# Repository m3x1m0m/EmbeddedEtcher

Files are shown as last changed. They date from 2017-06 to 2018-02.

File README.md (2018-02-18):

# Embedded Etcher
Design files related to a photo-sensitive layering method etching machine
everyone can build to produce prototypes quickly at home or in the lab.

## Architecture 
The etching machine consists basically out of two parts. The
first part is a UV light, which is used to develop a photo-sensitive PCB. Once
this has been done.  The PCB has to be treated with sodium hydroxide (NaOH)
dissolved in water. This removes the UV-sensitive plastic, where it has been
tackeled by the light. 

The second part is the actual etching machine, which is designed to be
compatible to euro cards (and even bigger ones). The etching machine is either
filled with sodium persulfate (Na<sub>2</sub>S<sub>2</sub>O<sub>8</sub>) or
iron(III) chloride (FeCl<sub>3</sub>) dissolved in water of course.

## RedheadOS

One of the byproducts of this project is a small real-time OS, which is ment to run on embedded platforms. It is based on fixed priority scheduling and includes some nice accessories, so one does not always have to reinvent the wheel for every new project.  

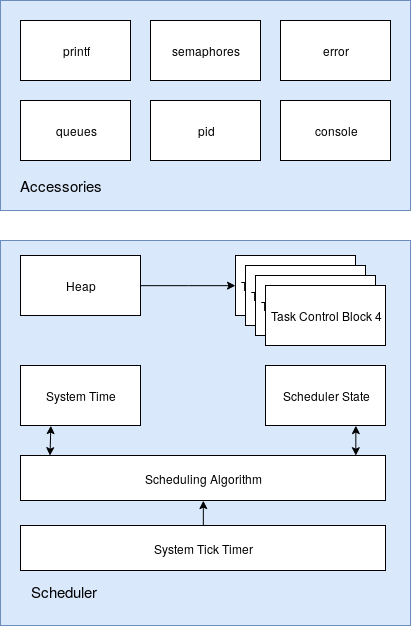
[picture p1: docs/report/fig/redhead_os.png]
ReadheadOS Structure.


## UV Light 

### Driver Extension Board

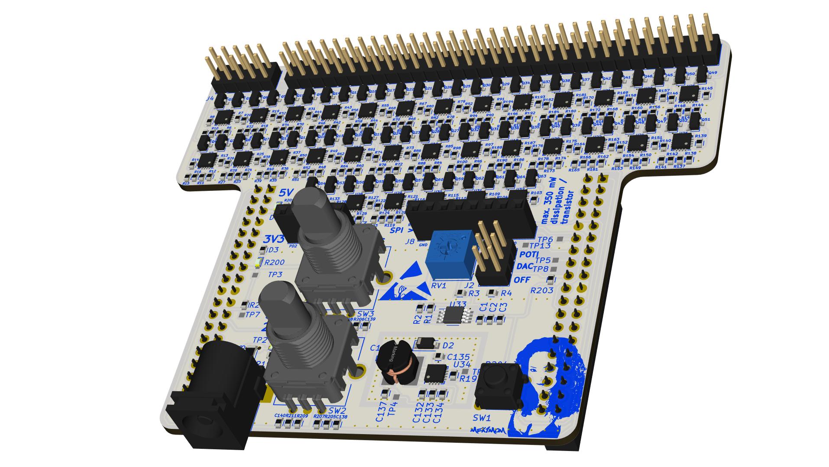
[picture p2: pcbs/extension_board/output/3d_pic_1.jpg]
3D Preview from KiCad (1).


This PCB is made to fit the [Nucleo-F103RB](http://www.st.com/en/evaluation-tools/nucleo-f103rb.html)
development board from STM. Features:
* 64 LED driver stages.
* 6.4 A (0.1 A per stage) and 24 V max. input.
* 0.2 A max. and 350 mW dissipation max. per stage. Stages can be left floating if unused without
the threat of damaging the device.
* 10 Bit Digital-to-Analog Converter (DAC) to steer the driver combined with feedback amplification
to achieve a tremendously fine resolution.
* Optional potentiometer to set the current.
* Control loop to guarantee the desired current and respond quickly to changing the setpoint.
* 2 rotary encoders and 1 tactile switch.
* I2C header.
* SPI header.
 
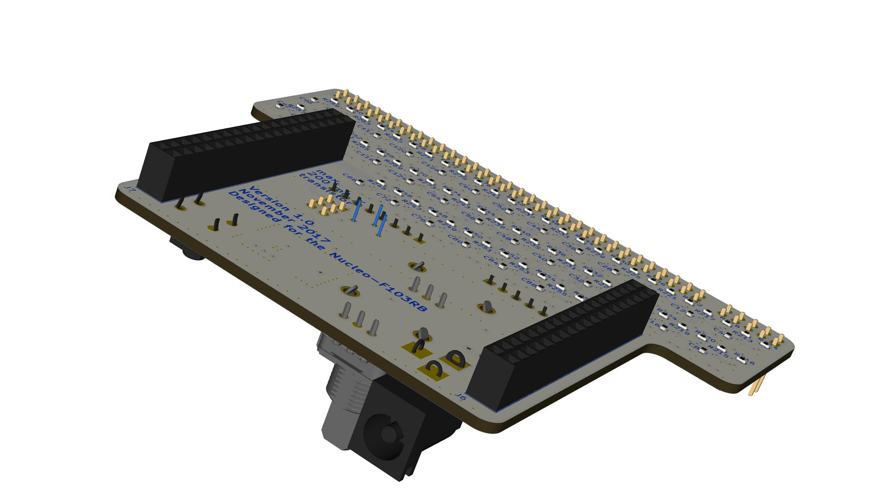
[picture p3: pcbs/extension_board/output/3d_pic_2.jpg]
3D Preview from KiCad (2).

  
  It is important to mention, that the resistors for the non-inverting amplifier
  in the feedback loop are optimized to result in a maximum current of 33 mA for
  3.3 V in order to achieve higher currents different resistor values have to be
  chosen.   
  
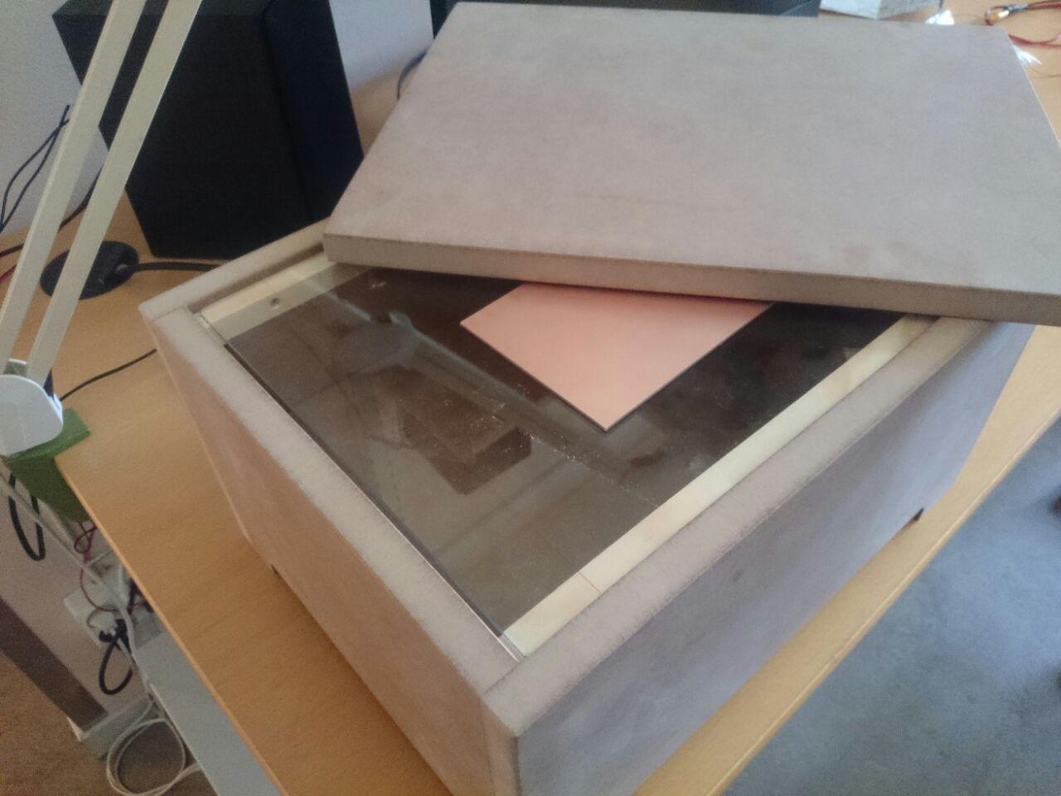
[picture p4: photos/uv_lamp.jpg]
UV Lamp
   

## Cuvette 

The cuvette can be handcrafted. It is possible to buy the five glass pieces need
at a glassers shop or to cut it oneself. The glass parts can be glued together with
silicon.  
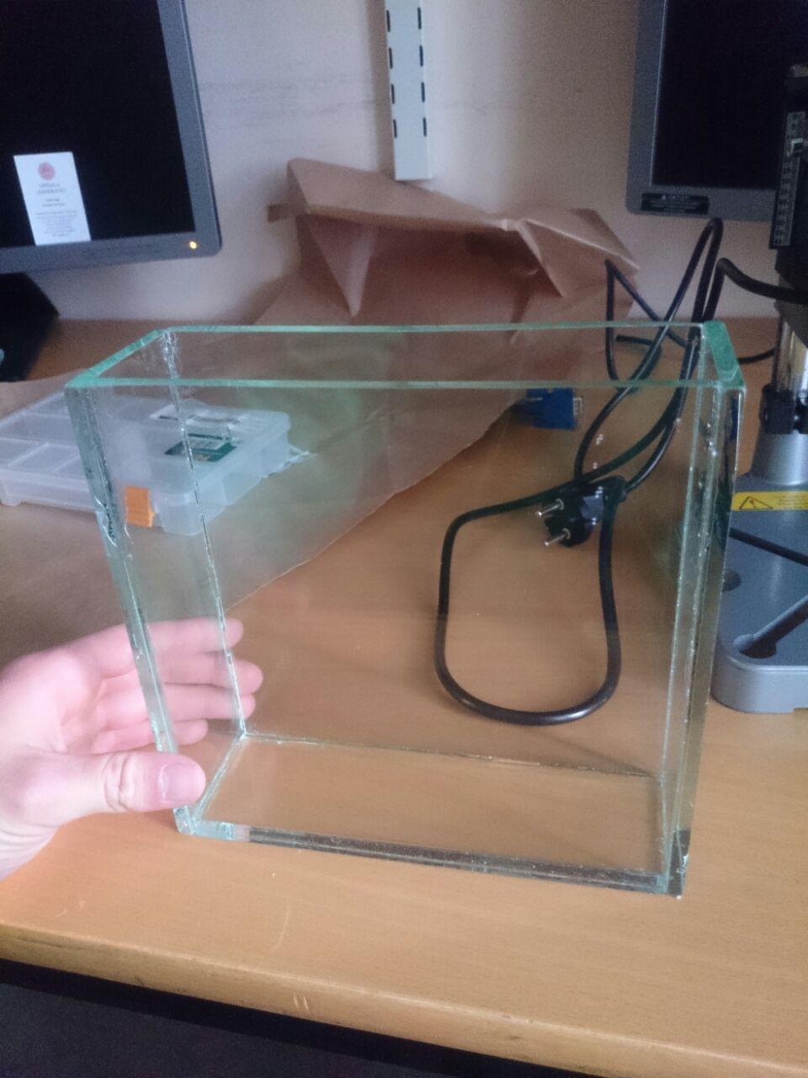
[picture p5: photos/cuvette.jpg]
Cuvette


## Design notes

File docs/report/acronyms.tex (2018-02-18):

%%%%%%%%%%%%%%%%%%%%%%%%%%%%%%%%%%%%%%%%%%%%%%%%%%%%%%%%%%%%%%%%%%%%%%%%%%%%%%%%%%%%%%
%% Author:      Nils Weber and Maximilian Stiefel
%% Date:        23.12.2017
%% University:  Uppsala Universitet
%% Department:  Institutionen för informationsteknologi 
%% Course:      Embedded Control System Project
%% Project:     PRECISELY CONTROLLED DIY ETCHING MACHINE 
%%				FOR USAGE AT HOME AND IN SMALL LABS
%%%%%%%%%%%%%%%%%%%%%%%%%%%%%%%%%%%%%%%%%%%%%%%%%%%%%%%%%%%%%%%%%%%%%%%%%%%%%%%%%%%%%%

\newacronym[firstplural={Printed Circuit Boards (PCBs)},plural={PCBs}]{PCB}{PCB}{Printed Circuit Board}
\newacronym[firstplural={Light Emitting Diodes (LEDs)},plural={LEDs}]{LED}{LED}{Light Emitting Diode}
\newacronym[firstplural={Integrated Development Environments (IDEs)},plural={IDEs}]{IDE}{IDE}{Integrated Development Environment}
\newacronym[firstplural={Task Control Blocks (TCBs)},plural={TCBs}]{TCB}{TCB}{Task Control Block}

\newacronym{DIY}{DIY}{Do It Yourself}
\newacronym{ECAD}{ECAD}{Electronic Computer-Aided Design}
\newacronym{UV}{UV}{Ultraviolet}
\newacronym{DC}{DC}{Direct Current}
\newacronym{PWM}{PWM}{Pulse-Width Modulation}
\newacronym{EMI}{EMI}{Electromagnetic Interference}
\newacronym{SPI}{SPI}{Serial Peripheral Interface}
\newacronym{I2C}{I2C}{Inter-Integrated Circuit}
\newacronym{OLED}{OLED}{Organic \gls{LED}}
\newacronym[firstplural={Operating Systems (OS)},plural={OS}]{OS}{OS}{Operating System}
\newacronym{DAC}{DAC}{Digital-to-Analog Converter}
\newacronym{ADC}{ADC}{Analog-to-Digital Converter}
\newacronym{IC}{IC}{Integrated Circuit}
\newacronym{NTC}{NTC}{Negative Temperature Coefficient}
\newacronym{PID}{PID}{Proportional Integral Differential}
\newacronym{USART}{USART}{Universal Asynchronous/Synchronous Receiver/Transmitter}
\newacronym{EEPROM}{EEPROM}{Electrically Erasable Programmable Read-Only Memory}
\newacronym{GNU}{GNU}{GNU's Not Unix!}
\newacronym{IRQ}{IRQ}{Interrupt Request}
\newacronym{FDM}{FDM}{Fused Deposition Modeling}

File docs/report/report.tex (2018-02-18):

%%%%%%%%%%%%%%%%%%%%%%%%%%%%%%%%%%%%%%%%%%%%%%%%%%%%%%%%%%%%%%%%%%%%%%%%%%%%%%%%%%%%%%
%% Author:      Nils Weber and Maximilian Stiefel
%% Date:        23.12.2017
%% University:  Uppsala Universitet
%% Department:  Institutionen för informationsteknologi 
%% Course:      Embedded Control System Project
%% Project:     PRECISELY CONTROLLED DIY ETCHING MACHINE 
%%				FOR USAGE AT HOME AND IN SMALL LABS
%%%%%%%%%%%%%%%%%%%%%%%%%%%%%%%%%%%%%%%%%%%%%%%%%%%%%%%%%%%%%%%%%%%%%%%%%%%%%%%%%%%%%%

\documentclass{report}

%%%%%%%%%%%%%%%%%%%%%%%%%%%%%%%%%%%%%%%%%%%%%%%%%%%%%%%%%%%%%%%%%%%%%%%%%%%%%%%%%%%%%%
% Preamble
%%%%%%%%%%%%%%%%%%%%%%%%%%%%%%%%%%%%%%%%%%%%%%%%%%%%%%%%%%%%%%%%%%%%%%%%%%%%%%%%%%%%%%

% Encoding of the input
\usepackage[utf8]{inputenc}

% Geometry stuff
\usepackage[head=24pt,a4paper,lmargin={2.5cm},rmargin={2.5cm},tmargin={2.5cm},
bmargin={2.5cm}]{geometry}

% For graphics
\usepackage{graphicx}
\usepackage{float}

% For code highlighting
\usepackage{minted}

% For shaded
\usepackage{xcolor}
\usepackage{framed}
\definecolor{shadecolor}{gray}{0.9}

% For some symbols
\usepackage{textcomp}
%\usepackage{eurosans}

% For math
\usepackage{amssymb}
\usepackage{amsmath}

\setlength{\parindent}{0em} 

% For title formatting 
\usepackage{titlesec} 

\titleformat%
{\chapter}%
[block]%
{\bfseries\Huge}%
{\thechapter\hspace{1cm}}%
{0pt}%
{\bfseries\Huge}%

% For SI units.
\usepackage{siunitx}

% Input definition macros
\input{mydefs.tex}

\usepackage{hyperref}
\hypersetup{
	plainpages=false,
	unicode=false,
	pdftoolbar=true,
	pdfmenubar=true,
	pdffitwindow=false,
	pdfstartview={FitH},
	pdftitle={\mytitle},
	pdfauthor={\myauthora ,\space\myauthorb},
	pdfsubject={\mytypeofwork\space\myduedate},
	pdfcreator={\myauthora ,\space\myauthorb},
	pdfproducer={\myauthora ,\space\myauthorb},
	pdfkeywords={\mykeywords},
	pdfnewwindow=true,
	pdfborder={0 0 0},
	colorlinks=false,
	linkcolor=black,
	citecolor=black,
	filecolor=black,
	urlcolor=cyan
}	

\newcommand{\newpar}{\vspace{1em}\\}
\newcommand{\myemph}[1]{\textsl{#1}}

% For PDFs
\usepackage{pdfpages}

% For quotes
\usepackage[autostyle]{csquotes}
\usepackage[style=ieee,backend=bibtex]{biblatex}
\addbibresource{literature.bib}

% For tables
\usepackage{tabularx}
% For a forced linebreak in a table cell 
% cf. https://tex.stackexchange.com/questions/2441/how-to-add-a-forced-line-break-inside-a-table-cell#19678
\newcommand{\specialcell}[2][c]{%
  \begin{tabular}[#1]{@{}c@{}}#2\end{tabular}}

% For glossary
\usepackage[toc,nonumberlist]{glossaries} 
\makeglossaries     
\input{./acronyms.tex}

% For chemical formulas
\usepackage{chemformula}

% Header and footer
\usepackage{fancyhdr}
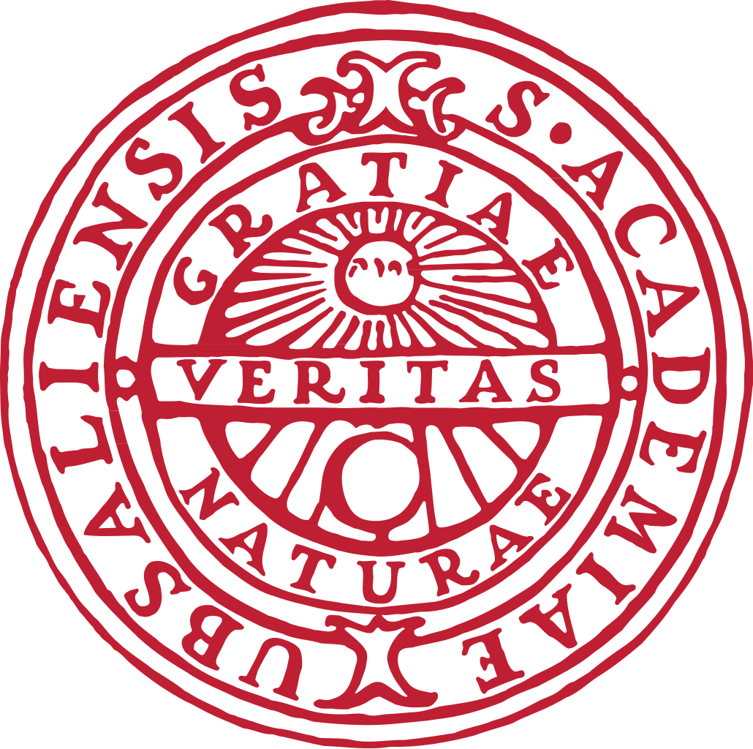
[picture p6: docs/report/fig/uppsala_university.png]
\lhead{\ifnum\value{chapter}>0  \fi}
\chead{}
\rhead{\ifnum\value{chapter}>0 
\leftmark{} |
\rightmark{}
\fi}
\lfoot{}
\cfoot{\thepage}
\rfoot{}
%\setlength{\headheight}{1cm}

\begin{document}

%%%%%%%%%%%%%%%%%%%%%%%%%%%%%%%%%%%%%%%%%%%%%%%%%%%%%%%%%%%%%%%%%%%%%%%%%%%%%%%%%%%%%%
% Titlepage
%%%%%%%%%%%%%%%%%%%%%%%%%%%%%%%%%%%%%%%%%%%%%%%%%%%%%%%%%%%%%%%%%%%%%%%%%%%%%%%%%%%%%%
\input{titlepage.tex}

\newcounter{roman}
\pagenumbering{Roman}

\pagestyle{fancy}

%%%%%%%%%%%%%%%%%%%%%%%%%%%%%%%%%%%%%%%%%%%%%%%%%%%%%%%%%%%%%%%%%%%%%%%%%%%%%%%%%%%%%%
% TOC etc.
%%%%%%%%%%%%%%%%%%%%%%%%%%%%%%%%%%%%%%%%%%%%%%%%%%%%%%%%%%%%%%%%%%%%%%%%%%%%%%%%%%%%%%
\tableofcontents
\listoffigures
\newpage
\listoftables
\printglossary[title=List of Abbreviations,toctitle=List of Abbreviations,type=\acronymtype]

\newpage
\setcounter{roman}{\value{page}}
\pagenumbering{arabic}
\setcounter{page}{1}

%%%%%%%%%%%%%%%%%%%%%%%%%%%%%%%%%%%%%%%%%%%%%%%%%%%%%%%%%%%%%%%%%%%%%%%%%%%%%%%%%%%%%%
% Introduction
%%%%%%%%%%%%%%%%%%%%%%%%%%%%%%%%%%%%%%%%%%%%%%%%%%%%%%%%%%%%%%%%%%%%%%%%%%%%%%%%%%%%%%

\input{./doc/introduction.tex}

%%%%%%%%%%%%%%%%%%%%%%%%%%%%%%%%%%%%%%%%%%%%%%%%%%%%%%%%%%%%%%%%%%%%%%%%%%%%%%%%%%%%%%
% Background and Analysis
%%%%%%%%%%%%%%%%%%%%%%%%%%%%%%%%%%%%%%%%%%%%%%%%%%%%%%%%%%%%%%%%%%%%%%%%%%%%%%%%%%%%%%

\input{./doc/background.tex}

%%%%%%%%%%%%%%%%%%%%%%%%%%%%%%%%%%%%%%%%%%%%%%%%%%%%%%%%%%%%%%%%%%%%%%%%%%%%%%%%%%%%%%
% Design
%%%%%%%%%%%%%%%%%%%%%%%%%%%%%%%%%%%%%%%%%%%%%%%%%%%%%%%%%%%%%%%%%%%%%%%%%%%%%%%%%%%%%%

\input{./doc/design.tex}

%%%%%%%%%%%%%%%%%%%%%%%%%%%%%%%%%%%%%%%%%%%%%%%%%%%%%%%%%%%%%%%%%%%%%%%%%%%%%%%%%%%%%%
% Implementation
%%%%%%%%%%%%%%%%%%%%%%%%%%%%%%%%%%%%%%%%%%%%%%%%%%%%%%%%%%%%%%%%%%%%%%%%%%%%%%%%%%%%%%

\input{./doc/implementation.tex}

%%%%%%%%%%%%%%%%%%%%%%%%%%%%%%%%%%%%%%%%%%%%%%%%%%%%%%%%%%%%%%%%%%%%%%%%%%%%%%%%%%%%%%
% Evaluation
%%%%%%%%%%%%%%%%%%%%%%%%%%%%%%%%%%%%%%%%%%%%%%%%%%%%%%%%%%%%%%%%%%%%%%%%%%%%%%%%%%%%%%

\input{./doc/evaluation.tex}

%%%%%%%%%%%%%%%%%%%%%%%%%%%%%%%%%%%%%%%%%%%%%%%%%%%%%%%%%%%%%%%%%%%%%%%%%%%%%%%%%%%%%%
% Conclusion
%%%%%%%%%%%%%%%%%%%%%%%%%%%%%%%%%%%%%%%%%%%%%%%%%%%%%%%%%%%%%%%%%%%%%%%%%%%%%%%%%%%%%%

\input{./doc/conclusion.tex}

%%%%%%%%%%%%%%%%%%%%%%%%%%%%%%%%%%%%%%%%%%%%%%%%%%%%%%%%%%%%%%%%%%%%%%%%%%%%%%%%%%%%%%
% Bibliography and Appendix
%%%%%%%%%%%%%%%%%%%%%%%%%%%%%%%%%%%%%%%%%%%%%%%%%%%%%%%%%%%%%%%%%%%%%%%%%%%%%%%%%%%%%%

\clearpage
\pagenumbering{Roman}
\setcounter{page}{\value{roman}}
\pagestyle{empty}

\printbibliography[heading=bibintoc]

%%%%%%%%%%%%%%%%%%%%%%%%%%%%%%%%%%%%%%%%%%%%%%%%%%%%%%%%%%%%%%%%%%%%%%%%%%%%%%%%%%%%%%
% Appendix
%%%%%%%%%%%%%%%%%%%%%%%%%%%%%%%%%%%%%%%%%%%%%%%%%%%%%%%%%%%%%%%%%%%%%%%%%%%%%%%%%%%%%%
\appendix
% Introduce new geometry to be able to have more space for appendix
\newgeometry{lmargin={2.5cm},rmargin={2.5cm},tmargin={0cm},bmargin={1,5cm}}
\includepdf[pages={1},scale=0.8,pagecommand=\chapter{Schematics Extension Board}\label{append:extension}]{./fig/schematics_extension_board.pdf}
\includepdf[pages={2-3, 35-37},scale=0.8,pagecommand={}]{./fig/schematics_extension_board.pdf}

\chapter{Technical drawings of PCB-holder}
\label{append:techDrawPCB}

\begin{figure}[H]
\centering  
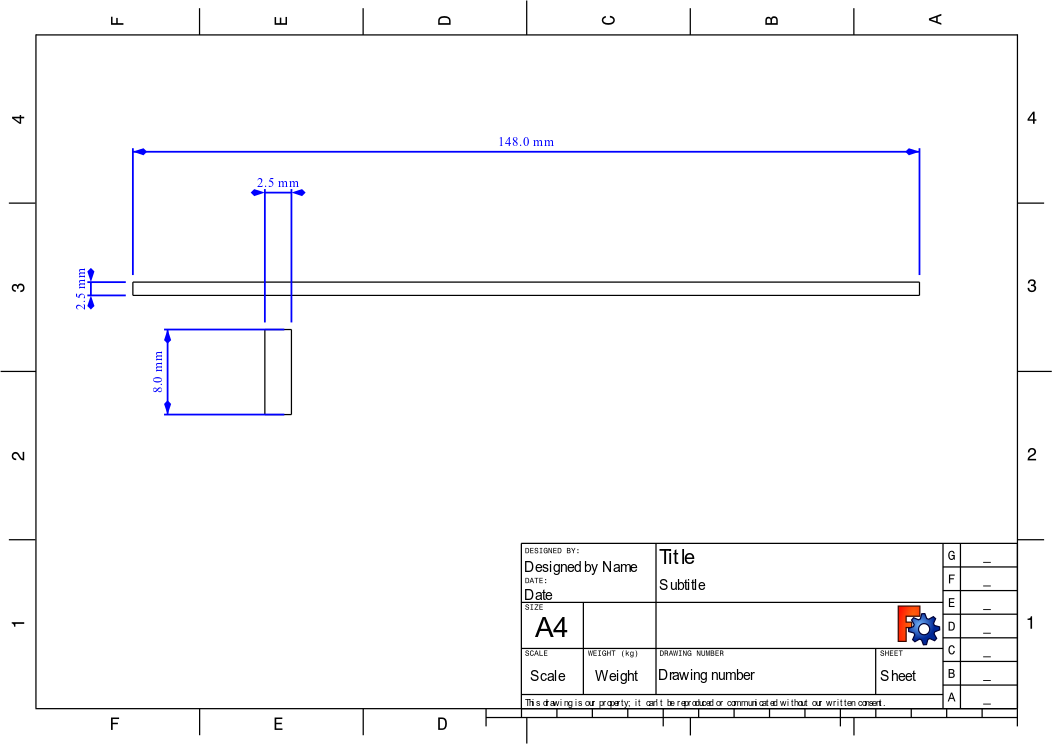
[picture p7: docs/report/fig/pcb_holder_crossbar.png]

\caption{Technical Drawing: Crossbar} 
\end{figure} 

\begin{figure}[H]
\centering  
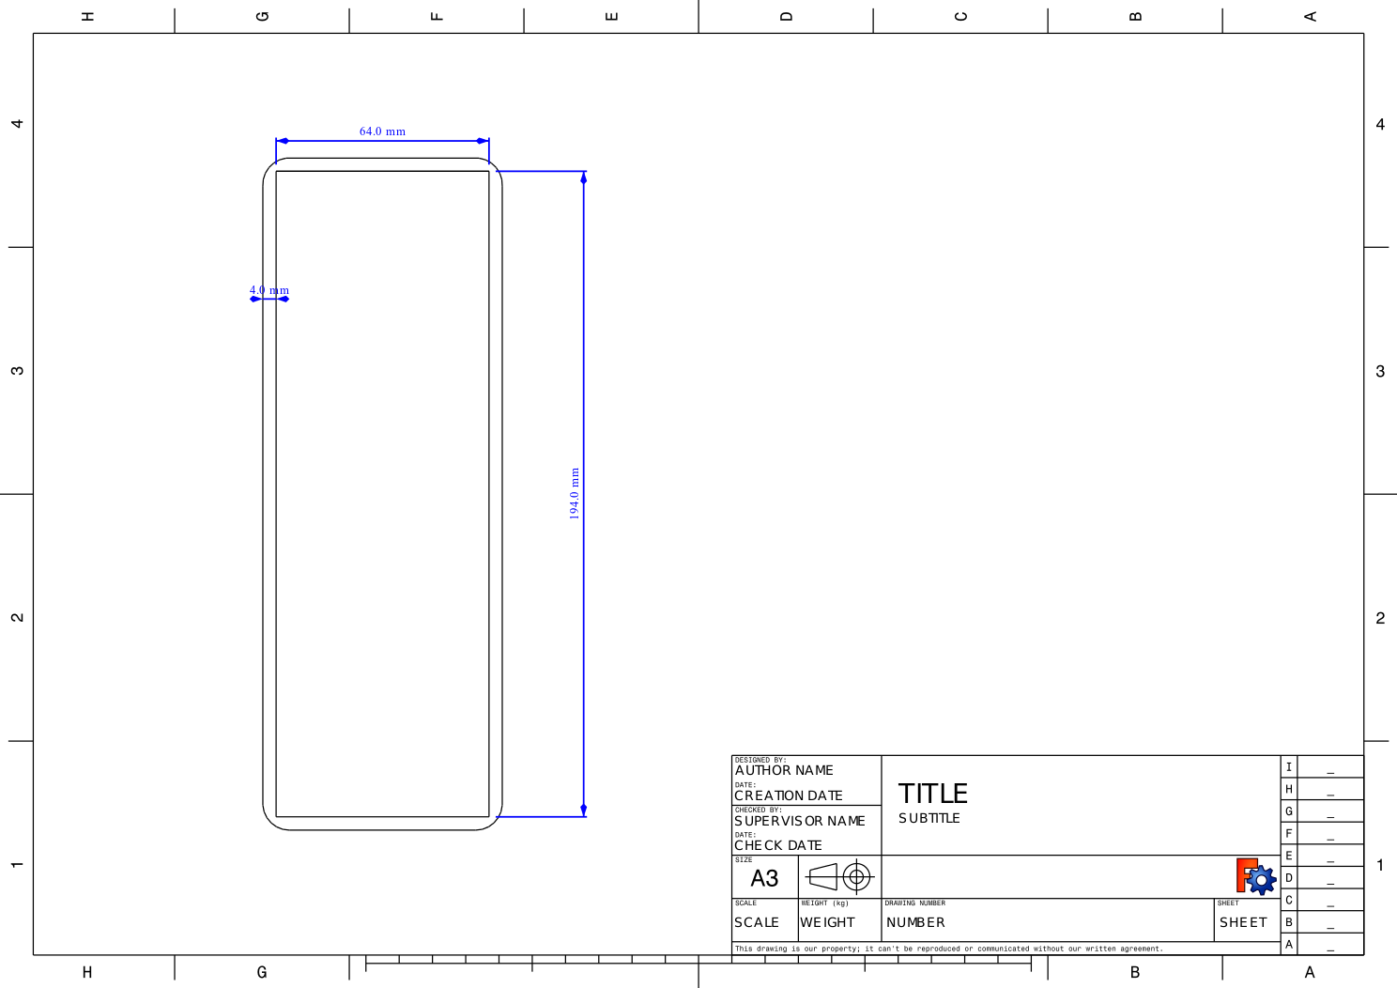
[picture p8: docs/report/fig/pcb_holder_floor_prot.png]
   
\caption{Technical Drawing: Floor}
\end{figure} 

\newgeometry{lmargin={2.5cm},rmargin={2.5cm},tmargin={2.5cm},bmargin={2.5cm}}

\begin{figure}[H]
\centering  
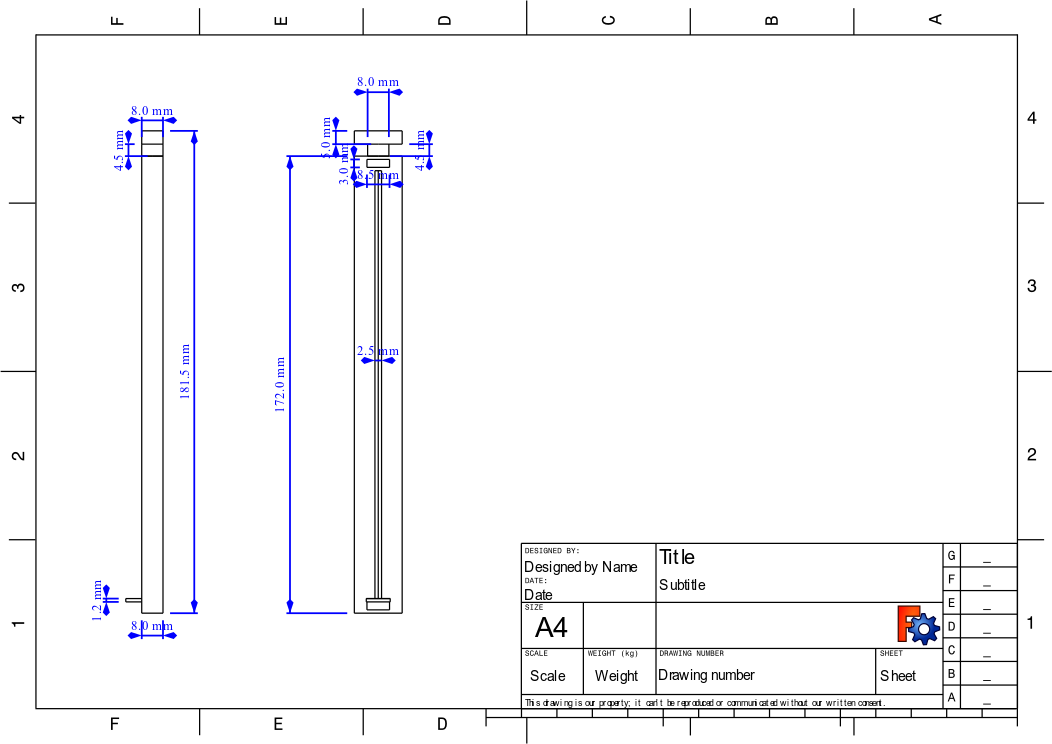
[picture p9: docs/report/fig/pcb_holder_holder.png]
   
\caption{Technical Drawing: Holder}
\end{figure} 

\begin{figure}[H]
\centering  
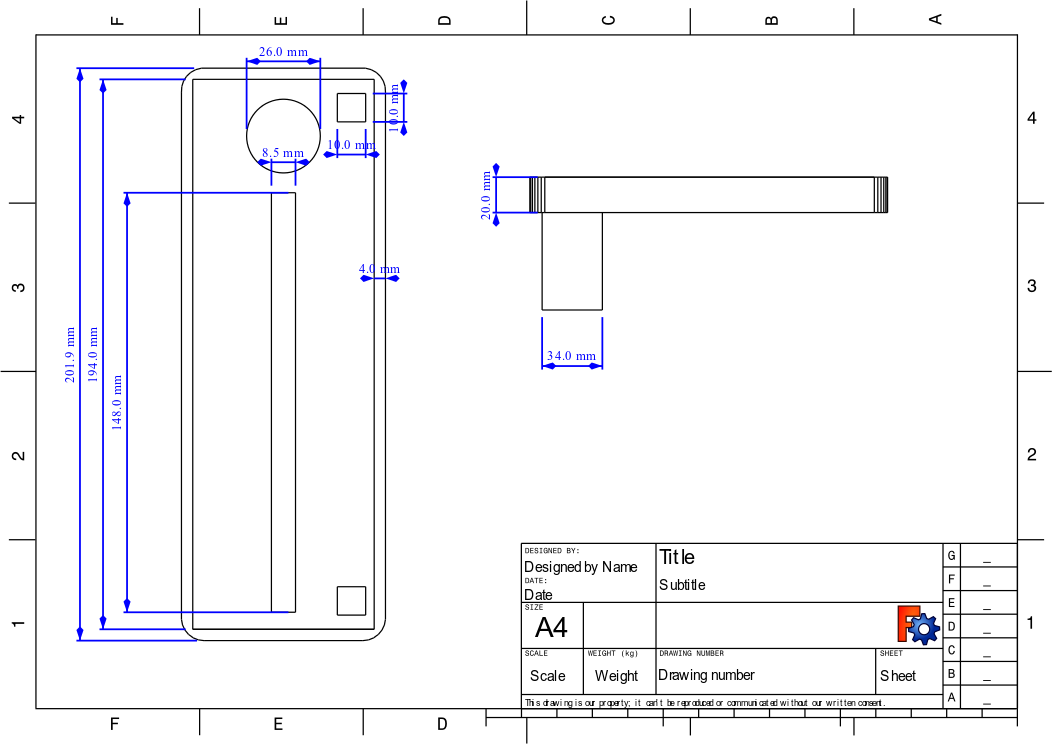
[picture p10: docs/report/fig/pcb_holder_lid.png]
  
\caption{Technical Drawing: Lid} 
\end{figure} 

\end{document}

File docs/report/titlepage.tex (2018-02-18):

%%%%%%%%%%%%%%%%%%%%%%%%%%%%%%%%%%%%%%%%%%%%%%%%%%%%%%%%%%%%%%%%%%%%%%%%%%%%%%%%%%%%%%
%% Author:      Nils Weber and Maximilian Stiefel
%% Date:        23.12.2017
%% University:  Uppsala Universitet
%% Department:  Institutionen för informationsteknologi 
%% Course:      Embedded Control System Project
%% Project:     PRECISELY CONTROLLED DIY ETCHING MACHINE 
%%				FOR USAGE AT HOME AND IN SMALL LABS
%%%%%%%%%%%%%%%%%%%%%%%%%%%%%%%%%%%%%%%%%%%%%%%%%%%%%%%%%%%%%%%%%%%%%%%%%%%%%%%%%%%%%%

\begin{titlepage}
% temporary margins only for titlepage
\newgeometry{lmargin={2cm},rmargin={2cm},tmargin={1cm},bmargin={2cm}}

%---------------------- University Logo-------------------------------------------
\begin{minipage}{\linewidth}
	\centering
    \begin{minipage}{0.49\linewidth}
    	\begin{figure}[H]
        	\hfill
		\end{figure}
	\end{minipage}
	\hfill
	\begin{minipage}{0.49\linewidth}
    	\vspace*{0.5cm}
    	\begin{huge}
    		\myuniversity\hfill
		\end{huge}
	\end{minipage}
\end{minipage}

%---------------------- Title ----------------------------------------------------
\vspace*{3em}
\begin{center}
  \noindent\rule{\textwidth}{1pt}
  \vspace*{0.3em}\\
  \huge\mytitle \\
  \noindent\rule{\textwidth}{1pt}

%---------------------- Other Info------------------------------------------------
  \vspace*{0.3em}
  \Large%
  {
    Project Report
    \vspace*{0.5cm}\\
    for the project course\\
    of Embedded Control Systems (1RT911)\\
    carried out in the \myperiod\\
    \vspace*{3em}
    Deadline: \myduedate
  }

%---------------------- Page Bottom ----------------------------------------------
\vfill
\begin{table}[H]
  \centering
  \begin{tabular}{ccc}
     \textbf{Student} & \textbf{Student} & \textbf{Supervisor} \\
     \myauthora &   \myauthorb & \mytutor  \\
     \myauthoramail &   \myauthorbmail & \mytutormail      
  \end{tabular}
\end{table}
  
\end{center}
\end{titlepage}

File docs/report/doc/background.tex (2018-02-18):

%%%%%%%%%%%%%%%%%%%%%%%%%%%%%%%%%%%%%%%%%%%%%%%%%%%%%%%%%%%%%%%%%%%%%%%%%%%%%%%%%%%%%%
%% Author:      Nils Weber and Maximilian Stiefel
%% Date:        23.12.2017
%% University:  Uppsala Universitet
%% Department:  Institutionen för informationsteknologi 
%% Course:      Embedded Control System Project
%% Project:     PRECISELY CONTROLLED DIY ETCHING MACHINE 
%%				FOR USAGE AT HOME AND IN SMALL LABS
%%%%%%%%%%%%%%%%%%%%%%%%%%%%%%%%%%%%%%%%%%%%%%%%%%%%%%%%%%%%%%%%%%%%%%%%%%%%%%%%%%%%%%

\chapter{Background and Analysis}
\label{chap:background}
% Talk about papers and available technology. Also put the results of the small market analysis here. 

\section{Market analysis}
\label{sec:marketanalysis}
% Homemade: http://sfprime.net/pcb-etching/
% Market-Overview 
% Bath ~500$: https://goo.gl/8ebNsr
% UV illuminator ~400$:
% https://www.ebay.com/itm/Uv-Licht-Hartende-Maschine-Tragbare-Neue-2Kw-F/232345844072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
There are already different commercial and non-commercial solutions on the market to realize small-scale \gls{PCB} etching. To find possible problems and optimization potential, in order to create a superior product, a small market analysis (see tab. \ref{tab:marketanalysis}) has been carried out in the in the run-up to the development phase of the project. 

\begin{table}[H]
\centering 
\begin{tabular}{p{0.25\textwidth} p{0.2\textwidth} p{0.15\textwidth} 
p{0.35\textwidth} } 
\textbf{Product}&
\textbf{Distributor / Manufacturer}&
\textbf{Price}& 
\textbf{Technical Data}\\\hline

\specialcell[t]{
AETZGERAET 1\\
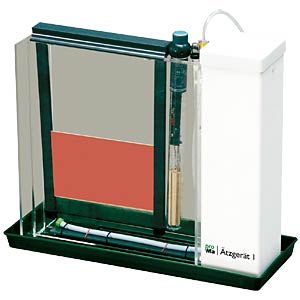
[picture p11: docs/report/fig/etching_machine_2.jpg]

}&
Reichelt / PROMA&
129.50 EUR (03.01.2018)&
Needed Acid Volume: 1.75 l. Max. PCB Size: 235 mm x 170 mm. Heating Power: 100 W. Air Pumping System included.\\ 

\specialcell[t]{
500-004 Universal Tank\\
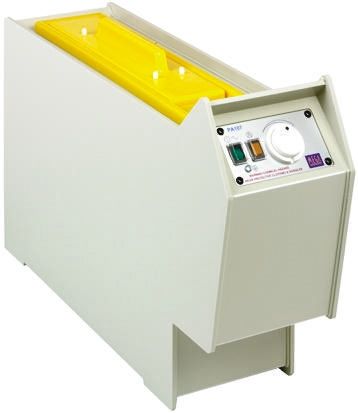
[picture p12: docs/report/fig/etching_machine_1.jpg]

}&
RS Components / Mega Electronics&
234.26 GBP (03.01.2018)&
Needed Acid Volume: 5 l. Max. PCB Size: 315 mm x 260 mm. Air Pumping System included\\\hline

\specialcell[t]{
UV-BELICHTER 1\\
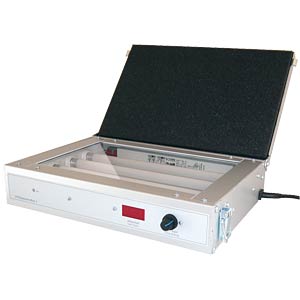
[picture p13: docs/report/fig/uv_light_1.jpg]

}&
Reichelt / PROMA&
219.7 EUR (03.01.2018)&
Timer included (0 - 100 min). Max. PCB Size: 160 mm x 250 mm. 4 x 8 W \gls{UV} tubes. Aluminium housing.\\

\specialcell[t]{
UV Exposure Unit\\
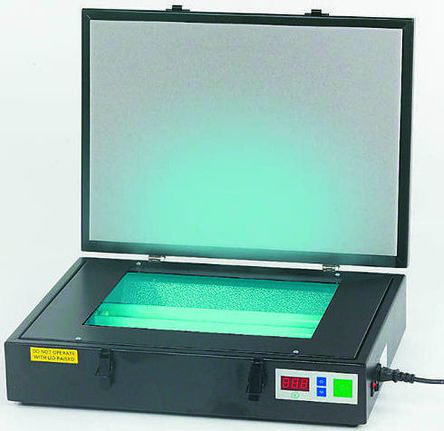
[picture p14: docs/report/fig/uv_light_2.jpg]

}&
RS Components / Mega Electronics&
183.32 GBP (03.01.2018)&
Timer included (0 - 6 min). Max. PCB Size: 150 mm x 245 mm. 2 x 8 W \gls{UV} tubes. Metal housing.\\

\hline
\end{tabular}
\caption{Market analysis.}
\label{tab:marketanalysis}
\end{table}

Talking about the etching machines, it is a fact, that all of them do have a heater and some sort of pump to accelerate the chemical reaction introduced in chapter \ref{chap:introduction}. 
\newpar
The \myemph{500-004 Universal Tank} from \myemph{RS Components} is quite big, usually too big for small scale production. For the etching process with sodium persulfate one uses \SI{220}{\gram\per\litre} with \SI{45}{\celsius} (cf. \cite{online:aetzen}). Using the tank from RS Components one needs \SI{1.1}{\kilo\gram} of sodium persulfate, which is neither really practical nor cheap, in case one only wants to etch a few \glspl{PCB} to e.g. test a microstrip bandpass filter. Nevertheless, the design looks really robust and justifies somehow the tough price. Also the maximum \gls{PCB} size is enormous or rather a bit too big for prototyping.
\newpar
The \myemph{AETZGERAET 1} from \myemph{Reichelt} has a way more competitive price, than its equivalent from \myemph{RS Components}. It also seems to be a bit more bodge. The maximum \gls{PCB} size is still impressive as well as the heater power. 
\newpar
Presumably, there is not really a sophisticated control mechanism keeping the temperature close to the setpoint. As far as one can derive this from the given technical data, the thermostats of both devices are based on a bimetal.
\newpar
The \gls{UV} lights are both functioning with \gls{UV} fluorescent tubes. Fluorescent tubes are considered hazardous as they contain mercury vapor, which is extremely toxic (cf. \cite{online:tubes}). For this reason there are plans to ban them in the European Union. It also seems, that one pays for the \gls{UV} light power (number of tubes).
\newpar
Both \gls{UV} light exposure machines have a timer to set the exposure time. This is clearly an important and necessary feature for such a machine as the development process parameters define the quality of the final etched result. Hence, the \gls{UV} light exposure time is an important factor to fine tune the etching result. 
\newpar
Two features neither the \myemph{UV Exposure Unit} from \myemph{RS Components} nor the \myemph{UV-BELICHTER 1} have: It is not possible to adjust the light intensity and the light does only come from one direction at a time. The second shortcoming can introduce problems, since one has to turn on the light, turn it off, turn the \gls{PCB} around and repeat the exposure process. Worst-case, this might lead to alignment problems (e.g. a mounting hole on one side does not align with a mounting hole on the other side). 
\newpar
The exposure units are both relatively pricey, which might be related to the metal housing. 
\newpar
To summarize one can name some ideas how to rectify shortcomings of the currently available products for prototype \gls{PCB} etching: 
\begin{itemize}
\item The etching tank shall not be bigger than \SI{2}{\litre}, as one needs more etching liquid, which is unnecessary for small-scale production. 
\item No expensive metal housings. 
\item It shall be possible, that the user or replicator picks the heater and the compressor for air bubbles flexibly. 
\item No mercury. 
\item Double-sided \gls{UV} light exposure.
\item Precisely controlled light intensity. 
\item Digital and elegant user interface. 
\end{itemize}

\section{LED Drivers}
\label{sec:leddrivers}

\subsection{Buck Converters}
\label{subsec:buck_conv}

\begin{figure}[H]                                                         
\centering          
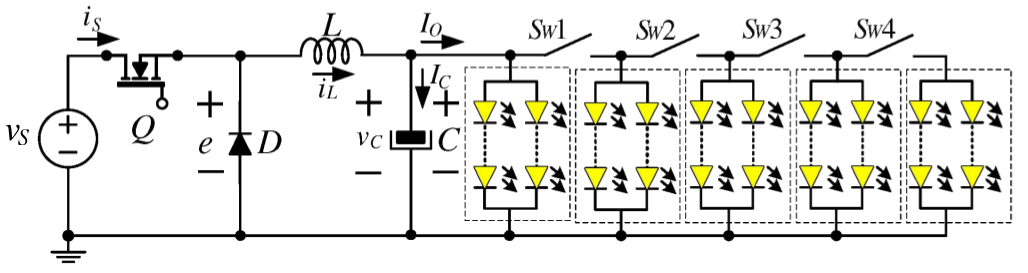
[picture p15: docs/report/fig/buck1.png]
   
\caption[Typcial buck converter as it can be found in a car.]{Typcial buck converter as it can be found in a car. Source: \cite{conference:buck1}.}   
\label{fig:buck1}                                                       
\end{figure}  

One of the ideas for improvements mentioned in section \ref{sec:marketanalysis} induces the use of \glspl{LED}. Therefore, in this section different state-of-the-art \gls{LED} driving techniques are introduced. To drive one \gls{LED} or a string of \glspl{LED} coupled in series one needs to keep the current constant for achieving constant light intensity. It is a well-known fact, that every single \gls{LED} differs concerning its electrical characteristics. The input to output transmission behavior i.e. \ensuremath{I(U)} differs from \gls{LED} to \gls{LED}. This is one challenge one has to master building a \gls{LED} driver. 
\newpar
A common approach, which is popular in automotive applications is a \myemph{buck converter} (cf. \cite{conference:buck1}). \myemph{Buck converters} leverage a switching-frequency to convert a high voltage into a lower voltage. In fig. \ref{fig:buck1} one can see, that in a car the current, which is drawn by the source can change rapidly, as for instance a rear light or an indicator is switched on. For this reason, a controller is needed to ensure, that enough current is provided even if rear light and indicator are switched on simultaneously. Buck converters are that popular because of their remarkable efficiency (greater than 90 \% is normal).
\newpar 
A buck converter from an electrical point of view switches between two states i.e. transistor \myemph{Q} is conducting (1) or non-conducting (2): 
\begin{enumerate}
\item If \myemph{Q} conducts \myemph{L} is directly connected to the voltage source. \myemph{C} and the load is connected to \myemph{L}. The energy stored in \myemph{L} increases. The current change results in a voltage across \myemph{L}, that counteracts the voltage of the source. This of course reduces the voltage over the load. 
\item If \myemph{Q} does not conduct \myemph{D} becomes conductive, because \myemph{L} is now a voltage source. The energy stored in the coil provides a current through the load. \myemph{L} discharges and the voltage across \myemph{L} drops again. The current through the load is still maintained. \myemph{C} helps to keep voltage and current through the load stable (close to \gls{DC} although a certain ripple is normal).  
\end{enumerate}
If the coil is charged and discharged quickly enough one can get into a steady state, where the output is within a certain range. The voltage is ramping up to a maximum and ramping down to a minimum. The output and possible input filters take care of converting this signal to a \gls{DC} signal. 
\newpar
One can also see the buck converter as a low-pass filter connected to a source with a square wave signal. The low-pass filter has ideally a cut-off frequency very close to \SI{0}{\Hz}. The filter excitation happens with a \gls{PWM} signal. One can easily explain how the steering of the current or voltage respectively works looking at the Fourier transformation of a rectangular pulse with a pulse width of \ensuremath{2\,t_0}. The pulse is defined as 
\begin{equation}
    x(t) = \begin{cases}
               1               & -t_0 \leq t \leq t_0\\
               0               & \text{otherwise}
           \end{cases}
\end{equation}
This function can be brought into the frequency domain using the most known equation of the heritage of Joseph Fourier. 
\begin{equation}
X(\omega) = \int_{-\infty}^{\infty} x(t) \cdot e^{-j \omega t} = \int_{-t_0}^{t_0} 1 \cdot e^{-j \omega t}
\end{equation}
Using \ensuremath{\int e^{at} = \frac{1}{a} e^{at}} leads to 
\begin{equation}
X(\omega) = \frac{1}{-j \omega} \, \bigl[ e^{-j \omega t_0} -  e^{j \omega t} \bigr] \text{ .}
\end{equation}
As the next step Euler's formula can be applied.
\begin{equation}
X(\omega) = \frac{2 sin(\omega t_0)}{\omega}  = \frac{2 t_0}{\omega} \frac{sin(\omega t_0)}{\omega t_0} = 2 si(\omega t_0)
\end{equation}
So what one ends up with the sinc function. As one tries to filter out every frequency except of \SI{0}{\Hz}, one can take a close look at \ensuremath{\omega = 0} with the help of l'H\^{o}spital's rule. 
\begin{equation}
\lim_{\omega \to 0} X(\omega) = \lim_{\omega \to 0} \frac{2 sin(\omega t_0)}{\omega} = \lim_{\omega \to 0} 2\,t_0\,cos(\omega t_0) = 2\,t_0  
\end{equation}
Hence, the absolute value of \ensuremath{X(\omega = 0)} becomes larger if the pulse length \ensuremath{t_0} becomes wider. This is why \gls{PWM} steering works. 

\begin{figure}[H]                                                         
\centering          
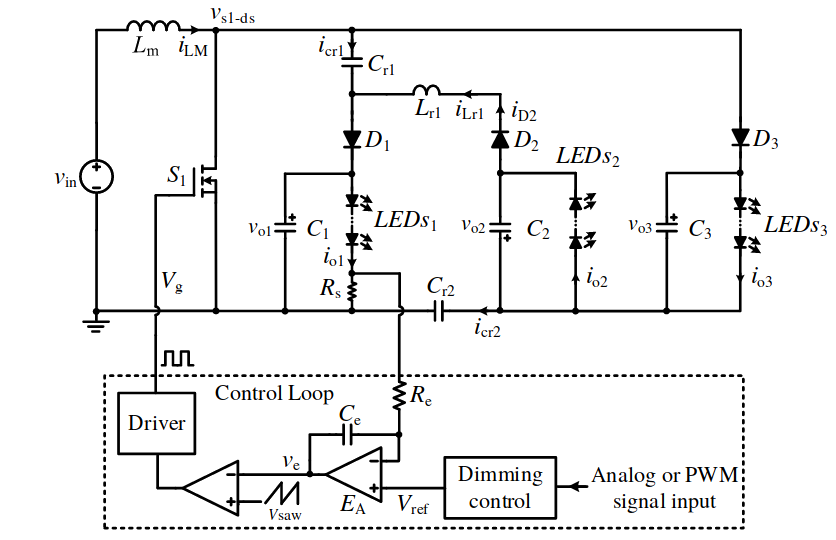
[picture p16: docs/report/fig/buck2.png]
   
\caption[More complex buck converter for automotive applications with analog control circuit.]{More complex buck converter for automotive applications with analog control circuit. Source: \cite{article:buck2}.}   
\label{fig:buck2}                                                       
\end{figure}  

In fig. \ref{fig:buck2} one can see a more complex draft of a buck converter with a analog controller. This circuit originates from \cite{article:buck2}. The first amplifier of the controller is an integrator. It adds memory to the control circuit. It also achieves, that the steering signal is somewhat proportional to the setpoint, which is what one can see analyzing the behavior: 
\begin{equation}
	V_e = - \frac{V_{ref}}{C_e R_e} \int V_{in} \, dt + A 
\end{equation}
whereas \ensuremath{A} is some constant. \ensuremath{V_{in} = R_s \cdot i_{o1}} is according to Ohm's law proportional to the current through the load (and a shunt resistor). The output of the first amplifier is fed into the second stage, a comparator. It compares the input with a sawtooth signal, which results in a \gls{PWM} with a duty cycle depending on the output of the first integrator. As the circuit analysis shows one deals with a proportional-integral controller here.   
\newpar 
Despite their tremendously superior efficiency, there are some disadvantages with buck converters like the switching frequency, that can cause \gls{EMI} problems. Comparing the different possibilities of buck converters one thing also becomes quite clear: Buck converters are complex. Moreover, they always need magnetic devices. Hence, designs become bulkier, less tightly integrated and more expensive if buck converters are used unnecessarily in places where they do not belong. For this reasons, linear regulators still have the right of existence nowadays. 

\subsection{Linear Regulators}
\label{subsec:buck_conv}

\begin{figure}[H]                                                         
\centering          
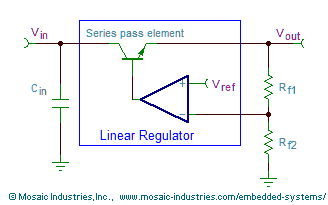
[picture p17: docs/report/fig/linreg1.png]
   
\caption[Typical linear regulator circuit.]{Typical linear regulator circuit. Source: \cite{online:linreg1}.}   
\label{fig:linreg1}
\end{figure}  

The other class of \gls{LED} drivers (power regulators) are linear regulators, which simply adjust their resistance in order to provide a constant current or voltage respectively. Unfortunately, a resistor converts electrical energy into heat, which is why linear regulators suffer from inefficiency, yet, they are very simple and one gets rid of possible \gls{EMI} problems caused by the switching frequency, that buck converters need. In fig. \ref{fig:linreg1} one can see a typical circuit of a linear regulator to provide a fixed voltage for a varying load impedance. This is a pure proportional controller.  

\section{Temperature Control}
\label{sec:temperatureControl}
Two approaches have been considered. Resources here can be money and time spent during development or operation.
\begin{enumerate}
\item Put more resources in sensors and save resources in the system model.
\item Put more resources in the controller model put save resources for sensors.
\end{enumerate}
The first approach was largely inspired by \cite{article:revLag}, where the application of the reversed lag principles are discussed for on-off control. A typical on-off control would result in cyclic temperature fluctuations like shown in fig. \ref{fig:waveforms}.

\begin{figure}[H]
\centering          
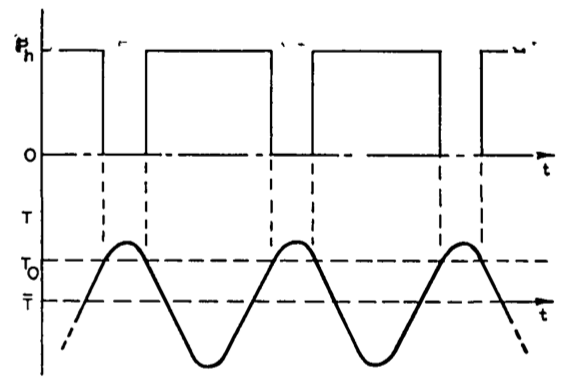
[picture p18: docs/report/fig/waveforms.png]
 \caption[Waveforms of heating power and temperature of a system with on-off control.]{Waveforms of heating power and temperature of a system with on-off control. Source: \cite{article:revLag}.}   
\label{fig:waveforms}
\end{figure}  

The paper shows that such a system can be improved by using two control elements which are completely immersed in the fluid of the enclosure. Thus, they are not affected by different errors. One of the two output signals has to have a lagging phase angle, which can be achieved by enclosing it "within a structure which ensures that its mean temperature is that of the fluid, but thermal transmission through the structure introduces a phase lag into the fluctuating component of the temperature of the element" \cite{article:revLag}. However, the circuitry of both sensors results in a leading phase angle of the enclosed sensor with respect to the directly immersed sensor. Thus, the next temperature can be "forseen" without the need of a system model. The paper concludes that "the principle of reversed lag can be applied to an on-off temperature-control system with useful but not spectacular reductions in the amplitude of the cyclic fluctuation in temperature" \cite{article:revLag}. Furthermore, two sensors would need to be purchased to acquire essentially the same data point, which spends more resources and thus contradicts the idea of a low-cost \gls{DIY} solution for small labs or at home.
\newpar
On-off controllers are known for their energy efficiency of their output systems, compared to amplifiers. That is especially true for high power control signals. Electro-heating systems, like the here considered system, are an example for such a system, which is characterized by large time constants. That lowers the need for high frequencies to keep proper parameters of the controlled signal further. The system's dynamics can be approximated with the following equation, where, \(k\) is the static gain, \(L\) is the time delay constant and \(T\) is the system time constant \cite{article:onoffPLC}.
\begin{align}
G(s)=\frac{ke^{-sL}}{1+sT}
\end{align}
A simple on-off controller leaves an static error, which can be reduced by increase of the controller hysteresis. However, this results in increasing the amplitude and period of the oscillation of the controlled signal. This is the disadvantage of this approach. 

The paper \cite{article:onoffPLC} further introduces an inertia corrector, to counteract the described disadvantage. "The hysteresis \(h\) of the controller is the only parameter that can affect the control quality in the basic control system." The new system model with inertia correction is shown in fig. \ref{fig:inertiaCorrection}. If the time constant of the inertia correction is much smaller than the time constant of the system, "then the controller with connected corrector exhibits features of proportional-derivative controller relative to the mean value of controlled signal" \cite{article:onoffPLC}.

\begin{figure}[H]
\centering          
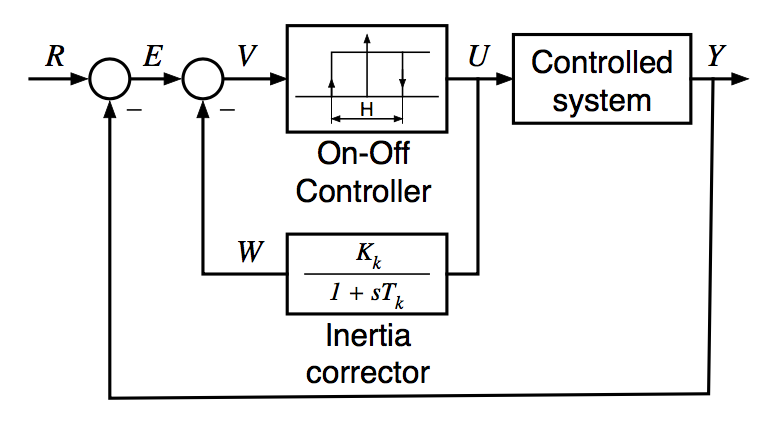
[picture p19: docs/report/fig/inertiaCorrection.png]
 \caption[The control system with unity negative feedback and inertia corrector.]{The control system with unity negative feedback and inertia corrector. Source: \cite{article:onoffPLC}.} 
\label{fig:inertiaCorrection}
\end{figure}  

However, as the authors of \cite{article:onoffPLC} show, the steady state error can be eliminated by using an additional corrector, instead of an integrator. This proportional corrector rescales the reference value to the range of 0 to 1, before entering the control comparator. The system has to be pre-identified, but the introduction makes the mean value of the controlled signal independent from any changes of the hysteresis \cite{article:onoffPLC}.

\begin{figure}[H]
\centering          
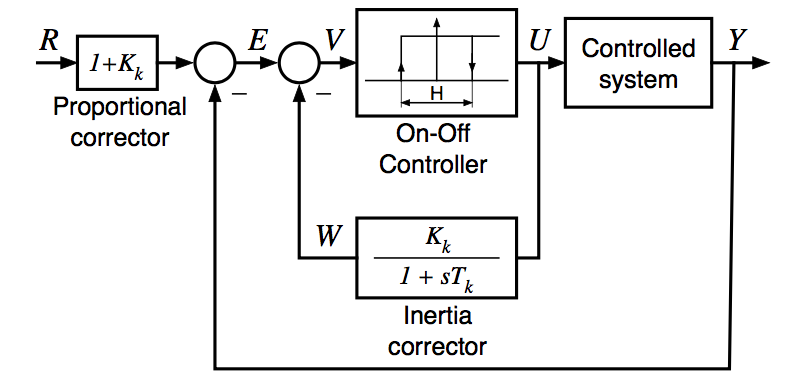
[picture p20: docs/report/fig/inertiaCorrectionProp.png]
 \caption[The control system with proportional and inertia correctors.]{The control system with proportional and inertia correctors. Source: \cite{article:onoffPLC}.} 
\label{fig:inertiaCorrectionProp}
\end{figure} 

The paper \cite{article:onoffPLC} concludes that the introduced control system "significantly reduces an amplitude of oscillation of controlled signal and shortens its period. An additional proportional corrector eliminates an error of the mean value of the controlled signal in the steady state."

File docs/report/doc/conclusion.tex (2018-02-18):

%%%%%%%%%%%%%%%%%%%%%%%%%%%%%%%%%%%%%%%%%%%%%%%%%%%%%%%%%%%%%%%%%%%%%%%%%%%%%%%%%%%%%%
%% Author:      Nils Weber and Maximilian Stiefel
%% Date:        23.12.2017
%% University:  Uppsala Universitet
%% Department:  Institutionen för informationsteknologi 
%% Course:      Embedded Control System Project
%% Project:     PRECISELY CONTROLLED DIY ETCHING MACHINE 
%%				FOR USAGE AT HOME AND IN SMALL LABS
%%%%%%%%%%%%%%%%%%%%%%%%%%%%%%%%%%%%%%%%%%%%%%%%%%%%%%%%%%%%%%%%%%%%%%%%%%%%%%%%%%%%%%

\chapter{Conclusion and Future Work}
\label{chap:conclusion}
% Summarize and conclude. Give a brief outlook as well on what will be done in future. 

The \gls{OS} kernel works and the system is ready to be deployed. A couple of accessories as are not implemented at all yet. Others need to be upgraded. The kernel is also subject to improvements. It shall be possible for the programmer to chose whether the scheduling is preemptive or non-preemptive. Also, it shall be possible to assign a stack size to a task and make sure it is not overflowed. 
\newpar 
The \gls{UV} light development put forth a complex four layer extension board for the \myemph{Nucleo-F103RB} from \myemph{STM}, including a sophisticated \gls{LED} driver using a linear regulator approach. The circuits on the board have been laid out, simulated and in a next step they will be tested. Moreover, a mechanical design has been sketched and built up. Unfortunately, it only supports single-sided \gls{UV} light exposure and causes a lot of manual work building it, which is something to be solved in the near future. One idea is to use some \gls{FDM} parts combined with two \glspl{PCB}, 128 \glspl{LED} each, to make double-sided exposure and an easy assembly possible. Most of the driver software implementation still has to be done and the whole system has to be integrated. 
\newpar
The temperature control development for the etching bath is ready for testing as soon as the temperature sensor is read correctly from the \gls{ADC}. These tests will show if the implemented improved on-off control will deliver sufficient results or if the heater has to be controlled with a constant current controller. When that is decided further steps regarding hardware design can be made.
Also, the current implementation has to be ported to the \gls{OS}, which should not entail much work, as it is structured in a fitting way already.

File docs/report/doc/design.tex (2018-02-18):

%%%%%%%%%%%%%%%%%%%%%%%%%%%%%%%%%%%%%%%%%%%%%%%%%%%%%%%%%%%%%%%%%%%%%%%%%%%%%%%%%%%%%%
%% Author:      Nils Weber and Maximilian Stiefel
%% Date:        23.12.2017
%% University:  Uppsala Universitet
%% Department:  Institutionen för informationsteknologi 
%% Course:      Embedded Control System Project
%% Project:     PRECISELY CONTROLLED DIY ETCHING MACHINE 
%%				FOR USAGE AT HOME AND IN SMALL LABS
%%%%%%%%%%%%%%%%%%%%%%%%%%%%%%%%%%%%%%%%%%%%%%%%%%%%%%%%%%%%%%%%%%%%%%%%%%%%%%%%%%%%%%

\chapter{Design}
\label{chap:design} 
\section{System Architecture and Required Functionality}
\label{sec:system_arch_and_req}
% Explain how our system is build up. 
First, the system consists out of two machines, the \gls{UV} light and the etching tank. Of course, these two machines are different and therefore need different designs. However, effort has been put into trying to use as many software and hardware components in both parts simultaneously to reduce the overall workload.  

\begin{figure}[H]                                                         
\centering          
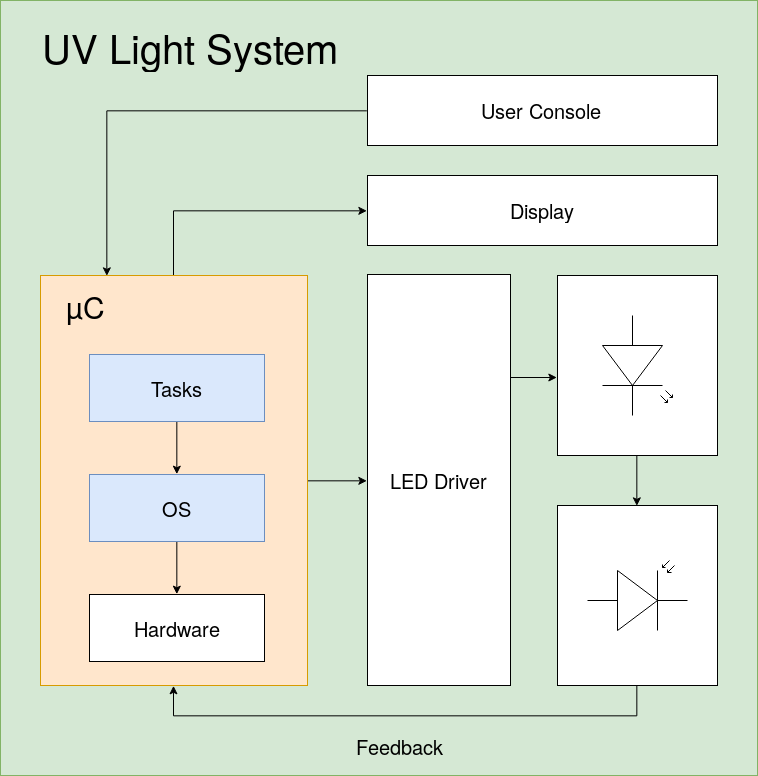
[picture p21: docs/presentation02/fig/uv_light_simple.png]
   
\caption[\mu C with user interface, custom LED driver and feedback loop.]{\mu C on the left executing tasks with an OS below. User interface is hooked up to the \mu C. Custom LED driver is connected to LEDs, steered by software. Feedback comes from a light sensor.}   
\label{fig:uv_light_simple}
\end{figure}  

In fig. \ref{fig:uv_light_simple} a rough sketch of the \gls{UV} light exposure unit is shown. The most important part is probably the \glspl{LED} and the driver for it. A feedback from the \glspl{LED} is generated with the help of a light sensor. This feedback can be coupled into a controller steering the driver. Besides the \gls{LED} driver, one needs a microcontroller, that executes the \gls{OS} and tasks to implement the desired functionality. In addition, some components for communication with the user are necessary, i.e. a console and a display. The user must be able to adjust exposure time and intensity. The intensity is not changeable with devices currently available on the market. 

\begin{figure}[H]                                                         
\centering          
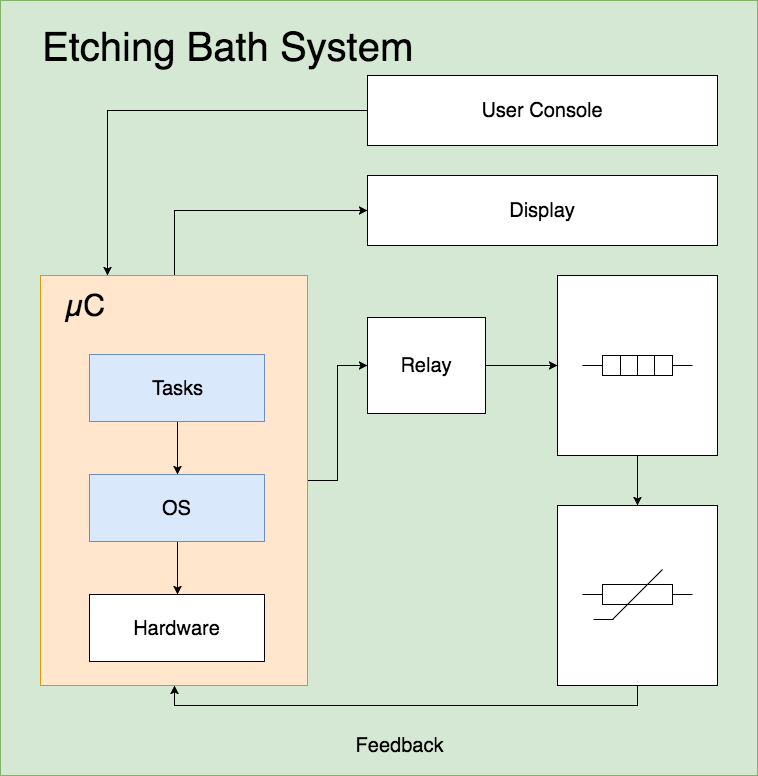
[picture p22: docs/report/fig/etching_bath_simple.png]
   
\caption[\mu C with user interface, heater and feedback loop.]{\mu C on the left executing tasks with an OS below. User interface is hooked up to the \mu C. The heater is connected via a relay, steered by software. Feedback comes from a temperature sensor.}   
\label{fig:etching_bath_simple}
\end{figure} 

In fig. \ref{fig:etching_bath_simple} the system architecture is sketched. Comparing to fig. \ref{fig:uv_light_simple} one can see many similarities, which result from the efforts to keep many parts of the system interchangable. The heater is not very sophisticated, thus the control is realized via a simple, optocoupled relay. An \gls{NTC} resistor is used as a temperature sensor and submersed into the etching bath. Thus, it closes the feedback loop for the control system.

Tab. \ref{tab:design_choices_uv_light} gives a bit more insights dealing with which components have been chosen and why. Also it includes information about the costs of each component. 

\section{Design Choices}
% Explain which design choices have been made and why.

The following table explains why different components have been chosen to enable the required functionality.

\begin{table}[H]
	\centering 
	\begin{tabular}{p{0.2\textwidth} p{0.2\textwidth} p{0.1\textwidth} 
		p{0.4\textwidth} } 
		\textbf{Block} &
		\textbf{Component(s)}&
		\textbf{Costs}& 
		\textbf{Justification of the
		Choice}\\\hline
		Microcontroller &
        STM32 microcontroller family &
        From 1.30 USD & 
        The µCs are cheap, because they are used everywhere. Open-source \glspl{IDE} are available and have a huge community. Open-source hardware is available as well. Big family tree with all kind of options. Powerful ARM Cortex-M0, Cortex-M3, Cortex-M4, Cortex-M7 32-bit processors. Ultra-low power (L-models) available. \\\hline 
        \gls{LED} Driver & 
        Custom designed linear regulator &
        0.40 USD per stage (25.60 USD for 64 stages) &
        One needs less components with a linear regulator (saves space and money). Choosing the voltage supply as close as possible to the voltage drop over the \gls{LED} or the \gls{LED} string, the efficiency is not too bad. Control part becomes very simple, yet effective. \\\hline
        Display &
        \gls{OLED} SSD1306 &
        2.50 USD &
        The display is cheap. Open-source driver software only needs to be ported to the platform. \gls{SPI} and \gls{I2C} interface available. \gls{OLED} technology is very elegant in comparison to alternatives.\\\hline
        User Console &
        Two rotary encoders and one tactile switch & 
        2 USD & 
        Very comfortable interface. One encoder for the exposure time, one for the light intensity and the tactile switch for starting the exposure process.\\
         &
        One rotary encoder including a push button & 
        \(<\) 1 USD & 
        Different parameters of the controller can be changed via the rotary encoder; the button is to switch between changing the parameter value or the parameter.\\\hline 
        Light Sensor &
        TSL2561 &
        1 USD & 
        Very easy to use with \gls{I2C} interface. Integrated amplifier. Very small. No need to develop a readout circuit with a photodiode.\\\hline 
        Temperature Sensor &
        NTCALUG01T103FL &
        3.5 USD & 
        Simple \gls{NTC} in metal package with ring connector. Robust, used in automotive applications. Comes with \SI{150}{\milli\metre} of wire. Detailed support from manufacturer.\\\hline
        Relay with optocoupler &
        - &
        \(<\) 1 USD & 
        Simple and safe to use via digital out.\\\hline 
        Air Temperature Sensor &
        SHT31 &
        4 USD & 
        Highly accurate air temperature and humidity sensor. Includes \gls{I2C}-interface.\\\hline
	\end{tabular}
	\caption{Design choices for the system: Why has each component been chosen?}
	\label{tab:design_choices_uv_light}
\end{table}

\section{Mathematical Model of the Tank}

Using the concept of energy balance to describe the thermodynamical model of the tank yields following equations \cite{online:mathModel}:
\begin{equation*}
Heat_{in} = Heat_{out} + Heat_{stored}
\end{equation*}

\begin{equation}
q_i=\frac{\theta_t - \theta_e}{R_{ta}}+c\frac{d\theta_t}{dt}
\end{equation}

with \(c\) as heat capacity of water, 4184\si{\frac{\joule}{\kilogram\kelvin}}, and
\(R_{ta}\) as temperature resistance between tank and ambient environment.

To further develop a model, different measurements are necessary. Water has a different specific heat capacity in different phases, i.e. as ice or water \cite{online:watercurve}.
\begin{equation}
q=m*C_s*\Delta T
\end{equation}

Different measurements to gather data to further build and understand the mathematical system. All measurements are to be done with the original water tank, heater and the temperature sensor.
\begin{itemize}
\item Cooling behavior 
	\begin{itemize}
	\item Measure temperature every 10s while cooling down water 
	\item Start from different temperatures
	\end{itemize}
\item Heating behavior
	\begin{itemize}
	\item Measure temperature every 10s while heating up water
	\end{itemize}
\item Determine time constants
\end{itemize}

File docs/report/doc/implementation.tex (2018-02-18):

%%%%%%%%%%%%%%%%%%%%%%%%%%%%%%%%%%%%%%%%%%%%%%%%%%%%%%%%%%%%%%%%%%%%%%%%%%%%%%%%%%%%%%
%% Author:      Nils Weber and Maximilian Stiefel
%% Date:        23.12.2017
%% University:  Uppsala Universitet
%% Department:  Institutionen för informationsteknologi 
%% Course:      Embedded Control System Project
%% Project:     PRECISELY CONTROLLED DIY ETCHING MACHINE 
%%				FOR USAGE AT HOME AND IN SMALL LABS
%%%%%%%%%%%%%%%%%%%%%%%%%%%%%%%%%%%%%%%%%%%%%%%%%%%%%%%%%%%%%%%%%%%%%%%%%%%%%%%%%%%%%%

\chapter{Implementation}
\label{chap:implementation}
% Explain explicitly how things have been implemented or are supposed to be implemented i.e. software, hardware, mechanics. 

\section{UV Light}
\label{sec:uv_light}

\begin{figure}[H]                                                         
\centering          
   
\caption[UV light system.]{UV light system. Top: Custom extension board. Bottom: Nucleo board with custom software.}   
\label{fig:uv_light_block_diagram}                                                       
\end{figure}  

The decision has been made to use the \myemph{Nucleo-F103RB}, a cheap (approx. 25 USD) development board, instead of designing a processor board. This has a couple of advantages:
\begin{itemize}
\item No \gls{PCB} design required to bring the STM32 on a board. 
\item Directly start programming without waiting until the hardware is ready.
\item Debugger and programmer from STM included. 
\item Time to develop something, that works is shortened. 
\end{itemize}
Instead, a custom extension board for the Nucleo board has been designed (cf. fig. \ref{fig:uv_light_block_diagram}). Everything has been laid out so the hardware can drive a lot of \myemph{industry standard T-1 3/4} \SI{5}{\milli\metre} \glspl{LED}. In fact it can supply 256 of these \glspl{LED}. Four \glspl{LED} can be put in series. The voltage drop does not exceed \SI{14}{\volt}. This has been verified by measurements in the lab with a current of \SI{30}{\milli\ampere}. Hence, a power supply of \SI{18}{\volt} is sufficient. Although something closer to \SI{14}{\volt} would be more efficient. However, it does not matter so much, as long as the linear regulator can dissipate enough power without being destroyed. 
\newpar
The \glspl{LED} are meant to be connected with a 64 pin header (low-side) and a 10 pin header to the board. Actually, a rather big housing has been built together to take in the \glspl{LED} and the electronics eventually. 
\newpar 
A small \gls{OS}, developed from scratch, runs on the STM32 to make real-time scheduling possible with a small code footprint and give a programmer all the necessary infrastructure to program conveniently (semaphores, queues, printf etc.). 

\subsection{Hardware}
\label{subsec:uv_light_hw}
\begin{figure}[H]                                                         
\centering          
   
\caption[Four layer extension board for the Nucleo-F103RB.]{Four layer extension board for the Nucleo-F103RB to drive 64 \gls{LED} channels. All 3D models have been entered into the \gls{ECAD} program to prevent unintended surprises.}   
\label{fig:3d_pic_pcb}                                                       
\end{figure}  
The board shown in fig. \ref{fig:3d_pic_pcb} has been developed and produced in the course of this project. It has four layers, but no micro vias, to, on the one hand get a grip on the complexity, and on the other hand save money (micro vias are still expensive than through-hole vias in production, cf. \ref{chap:introduction}). As an introduction, one can briefly list the features of this sophisticated piece of hardware.
\begin{itemize}
\item 64 \gls{LED} driver stages.
\item \SI{6.4}{\ampere} (\SI{0.1}{\ampere} per stage) and \SI{24}{\volt} max. input. 
\item \SI{0.2}{\ampere} max. and \SI{350}{\milli\watt} dissipation max. per stage. Stages can be left floating if unused without the threat of damaging the device. 
\item 10 Bit \gls{DAC} to steer the driver combined with feedback amplification to achieve a tremendously fine resolution. 
\item Optional potentiometer to set the current. 
\item Control loop to guarantee the desired current and respond quickly to changing the setpoint. 
\item 2 rotary encoders and 1 tactile switch.
\item \gls{I2C} header.
\item \gls{SPI} header. 
\end{itemize}

In appendix \ref{append:extension} an extract of the schematics of the board is available. The following lines shall briefly describe the different circuits. One page 1/37 one can see, that there are four main modules: The interface to the processor board, the \gls{LED} driver, the power management and  the user interface. 
\newpar 
On page 2/37 one can see the \gls{LED} driver part. On the right side, the \myemph{DAC101C085} from \myemph{Texas Instruments} is placed. \SI{0}{\ohm} resistors give flexibility in setting the bus address. The reference voltage is connected to the supply voltage of \SI{3.3}{\volt}, provided by the processor board. Below that, one can see a potentiometer and a connector, that can be populated with a jumper to set the reference voltage for the driver accordingly. The reference voltage is translated into a current whereas with the resistor configuration so far \SI{1}{\volt} equals \SI{10}{\milli\ampere}. The last connector on the right side is to make the \gls{I2C} interface 1 of the microcontroller accessible.
On the left side there are 32 times 2 driver stages, which equals a total of 64 driver stages. The group forming is as it is, because the deployed quadruple operational amplifier (\myemph{LM324}) can be used for 2 stages as it has four operational amplifiers inside. In addition, one can see the big 64 pin header for \gls{LED} connection. 
\newpar 
Page 3/37 reveals the \gls{LED} driver design as it shows one driver stage, which consists out of one \myemph{LM324} (four operational amplifiers) and two \myemph{MBT3904} (NPN transistor). The controller works as follows: 
\begin{enumerate}
\item A current \ensuremath{I_C} flows through the transistor into the shunt resistor \ensuremath{R_S}, which is connected to the input of a non-inverting amplifier. 
\item The shunt resistor \ensuremath{R_S} has a small resistance value of \SI{10}{\ohm} and translates the current \ensuremath{I_C} into a voltage \ensuremath{V_S = I_C \cdot R_S}. This might even work with a smaller shunt resistor. 
\item Obviously, the resulting voltage \ensuremath{V_S} is very small, which is why there is an amplifier in the feedback loop. Analyzing this operational amplifier configuration one ends up with the following relation between input and output: 
\begin{equation}
V_{out} = V_{in} \frac{R_1 + R_2}{R_1} = V_{in} \frac{\SI{20}{\kilo\ohm} + \SI{180}{\kilo\ohm}}{\SI{20}{\kilo\ohm}} = 10 V_{in}
\end{equation}
The size of the shunt resistor and the amplification factor determine the mapping between bits set in the \gls{DAC} (10 Bits) and the current through the \gls{LED}. Making the shunt resistor smaller is of course better because of unnecessary heat dissipation, but one has to keep in mind, that the operational amplifier is absolutely low-cost and has a certain offset voltage. Also, the closer one gets to the power supply voltages of the operational amplifier, the more problems of non-linearity occur. 
\item In the last step, the voltage output of the first stage is compared with the setpoint, coming either from the \gls{DAC} or the potentiometer. The output of the second stage is a current \ensuremath{I_B} proportional to the difference between the inputs. 
\begin{equation}
 I_C = I_B \cdot \beta
\end{equation}
is the relation between the base current and the collector current. According to the datasheet \ensuremath{\beta} is somewhere between 100 and 300, which is why a small error is neglected, since \ensuremath{I_C \gg I_B}: The current into the transistor collector is not the same as the current going out of the emitter. Hence, the current through the \glspl{LED} is about less then 1 \% smaller than the current the controller is aware of. 
\end{enumerate} 
The power distribution becomes clear taking a look at page 35/37. Using a barrel jack a lot of standard power supplies can be interfaced with the board. The board design is \myemph{IPC 2221} compliant given the parameters one can see in the schematics. A powerful buck converter \gls{IC} the \myemph{TS30011} steps down the input voltage to \SI{5}{\volt}. The processor board can be powered with external \SI{5}{\volt}, assumed that configured correctly. \SI{3.3}{\volt} can then be obtained from the processor board to supply e.g. the \gls{DAC} or the \gls{OLED} screen on the extension board. 
\newpar 
Page 36/37 shows the interfacing between processor and extension board. Nothing to really see here. 
\newpar 
The small user interface is on the last page 37/37. One connector enables access to the \gls{SPI} 1 of the microcontroller. Also one finds the tactile switch and two rotary encoders, which are debounced hardware wise. 

\subsection{Software}
\label{subsec:uv_light_sw}

\begin{figure}[H]                                                         
\centering          
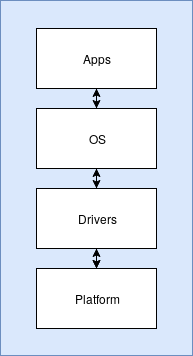
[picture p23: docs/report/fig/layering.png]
   
\caption[Layered code structure]{Layered code structure}   
\label{fig:layering}                                                       
\end{figure}

Fig. \ref{fig:layering} shows how the code ought to be structured in general. This allows to migrate the actual functionality quickly to another platform. However, as it turned out it can be hard sometimes not run into layer breaches i.e. the code one layer is supposed to only communicate with the layer above and the layer below if implemented properly.  
\newpar 
Every kind of controller is implemented in the \myemph{App layer}. The \gls{OS} layer provides a \gls{PID} controller infrastructure. A task is running, which handles the controller for the \gls{UV} light intensity, that gets the feedback input from the light sensor and steers the \gls{DAC}.
\newpar 
The \gls{DAC} driver is implemented in the \myemph{Driver layer}, whereas this driver needs to use \gls{I2C}, which is a hardware component of the \myemph{STM32}. \gls{I2C} is for this reason located in the \myemph{Platform layer}. Switching to another microcontroller, one ideally only needs to change the \myemph{Platform layer}. 
\newpar 
The \gls{OLED} screen driver belongs into the \myemph{Driver layer} accordingly and there are tasks to handle the user input from the rotary encoders and the switch in the \myemph{App layer}.  

\subsection{Mechanics}
\label{subsec:uv_light_mechanics}

\begin{figure}[H]                                                         
\centering          
   
\caption[Wooden box for the \gls{UV} exposer unit.]{Wooden box for the \gls{UV} exposer unit with 16 x 16 \gls{LED} matrix.}   
\label{fig:uv_lamp_box}                                                       
\end{figure} 

In cooperation with a carpenter a wooden box has been build, which uses a glass plate from an old scanner (cf. fig. \ref{fig:uv_lamp_box}). A wooden plate is located below the glass. On this wood plate there is a matrix out of 256 \glspl{LED}. The distance between glass and \gls{LED} matrix can be varied with the help of IKEA parts, that are plugged into the sidewalls while simultaneously holding the \gls{LED} matrix. The cabling, drilling and soldering to create the \gls{LED} matrix is a nightmare as one can imagine. Each single \gls{LED} needs to be connected to wires to lengthen the legs of it. Subsequently, every \gls{LED} is fixed in a hole and fixed with a hot glue gun. Always four \glspl{LED} have to be connected together in series. Eventually, every single one of the 64 stages has to be connected somehow to the extension board. For this reason a small adapter \gls{PCB} has been constructed (cf. fig. \ref{fig:adapter_board}). This board can be installed with wood screws and high- and low-side of the \glspl{LED} can be soldered. Following, one just has to plug in the two ribbon cables.   

\begin{figure}[H]                                                         
\centering          
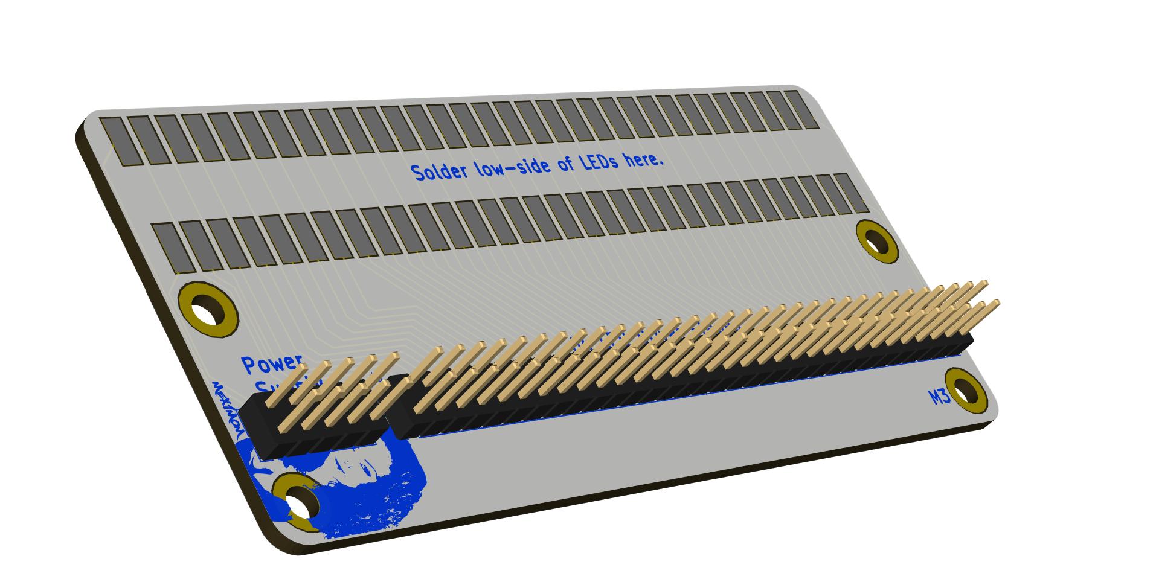
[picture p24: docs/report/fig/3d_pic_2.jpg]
   
\caption[Adapter board for \gls{LED} matrix enables simple plug and play.]{Adapter board for \gls{LED} matrix enables simple plug and play after soldering high- and low-side of the \gls{LED} strings.}   
\label{fig:adapter_board}                                                       
\end{figure} 

\section{Etching Tank}
\label{sec:etching_tank}
As briefly outlined in section \ref{sec:uv_light}, the Nucleo-F103RB has been chosen. During the development of the temperature control the Nucleo-L073RZ has been used for the simple reason of immediate availability. This led to more complications that originally anticipated, as discussed later in chapter \ref{chap:evaluation}.

\subsection{Hardware}
\label{subsec:etching_tank_hw}
Less sophisticated is the electric hardware for the temperature control, as it is in early prototyping stage to date and future tests will provide knowledge to chose the smartest path in further developments.
As shown earlier in fig. \ref{fig:etching_bath_simple} the system output is a 50W heater which is controlled via a relay. Its power source is a common power outlet of 230VAC. This relay is optocoupled to a normal digital output GPIO for security reasons.
For the user interface a small OLED screen with the SSD1306 driver and I2C interface is used as output, and a rotary encoder is used as input. The screen shows the temperature inside the etching bath, the reference temperature and the ambient temperature.
Since no cooling mechanism is installed, the reference temperature cannot be set below the ambient temperature.

\subsection{Software}
\label{subsec:etching_tank_sw}
Core of the system is the control algorithm implemented as described in \cite{article:onoffPLC}. The algorithm shown in fig. \ref{fig:inertiaCorrectionProp} has been implemented in \myemph{c} and is briefly described in the following. The names of the variables are chosen 
according to \cite{article:onoffPLC}.

A simple on-off controller is of course the heart of the algorithm. It determines a binary output based upon the corrected control error \(V\) and the hysteresis \(H\).

\begin{minted}[baselinestretch=1, fontsize=\small, linenos,frame=single,framesep=5pt]{C}
uint8_t onOffController(double iV, double iH) {
  uint8_t oU = 0;

  if (iV >= (iH/2)) {
    oU = 1;
  }
  else if (iV <= (iH/2)) {
    oU = 0;
  }

  return oU;
}
\end{minted}

The above described on-off controller is embedded in the following function, which would be called from the main program or called in a periodic task.
At first, the input parameters are re-scaled using the function \texttt{u\_map()} shown further below. The negative feedback is re-scaled to a ranged from 0 to 1, while the reference value is scaled to 0 to 100.
After the re-scaling the algorithm computes the proportional correction and calculates the control error based upon that value.
Next, the inertia correction is applied to the current value using the inertia correction value from the previous computation.
Now the on-off controller is called with the modified values from proportional and inertia corrections.
As a last step before returning the binary output value, the next inertia correction value is computed calling the respective function described below.

\begin{minted}[baselinestretch=1, fontsize=\small, linenos,frame=single,framesep=5pt]{C}
uint8_t controller(uint8_t _nowT, uint8_t _aimT) {
  double deltaT = 1; // HAS TO BE DETERMINED!!
  double K_k = 10.0;
  double T_k = 0.01;
  double H = 1; // HAS TO BE DETERMINED!!

  double A = (deltaT*K_k)/T_k;
  double B = 1-(deltaT/T_k);

  static double nW; // keep inertia correction value

  // re-scale input parameters
  double nY = ((double) u_map(_nowT, 0, 100, 0, 100))/100;
  double nR = (double) u_map(_aimT, 0, 100, 0, 100);

  // proportional correction
  double nP = nR * (1+K_k); // C = 1 + K_k

  // calculate error
  double nE = nP - nY;

  // apply inertia correction
  double nV = nE - nW;

  // call on-off controller
  uint8_t bU = onOffController(nV, H);

  // call inertia correction
  nW = inertiaCorrection(bU, nW, A, B);

  return bU;
}
\end{minted}

Following equation is implemented in the inertia correction function.
\begin{equation}
W_{t(i)} = AU_{t(i-1)}+BW_{t(i-1)}
\end{equation}
where
\begin{align}
A&=\frac{\Delta t K_k}{T_k} \\
B&=1-\frac{\Delta t}{T_k}
\end{align}

\begin{minted}[baselinestretch=1, fontsize=\small, linenos,frame=single,framesep=5pt]{C}
double inertiaCorrection(uint8_t fU, double nW, double A, double B) {
  double UA, WB;
  UA = ((double)fU)*A;
  WB = nW*B;

  return (UA+WB); //nW
}
\end{minted}

\begin{minted}[baselinestretch=1, fontsize=\small, linenos,frame=single,framesep=5pt]{C}
uint32_t u_map(uint32_t x, uint32_t in_min, uint32_t in_max, 
			   uint32_t out_min, uint32_t out_max) {
  return (x - in_min) * (out_max - out_min) / (in_max - in_min) + out_min; 
  }
\end{minted}

Other than that, the rotary encoder is implemented to easily adjust the wanted temperature. Both, the realtime and wanted temperature are shown on the display via I2C.

\subsection{Mechanics}
\label{subsec:etching_tank_mechanics}

The etching tank has been produced of a mix of glass and additive manufactured plastic parts to add functionality and form.
The lid and floor are shown in fig. \ref{fig:lidFloor}. Between lid and floor is a tank made of glass, seen in fig. \ref{fig:tank}. Inside this tank, hanging from the lid, is a U-shaped system to hold the PCB. Its size is adjustable to the PCB and maximum 148 mm x 160 mm. The technical drawings are attached in appendix \ref{append:techDrawPCB}. On the right side one can also see the heater and in the bottom a thinner black tube. This tube is connected to a compressor and ejects the air bubbles to speed up the removal of copper from the PCB.

\begin{figure}[H]
\centering          
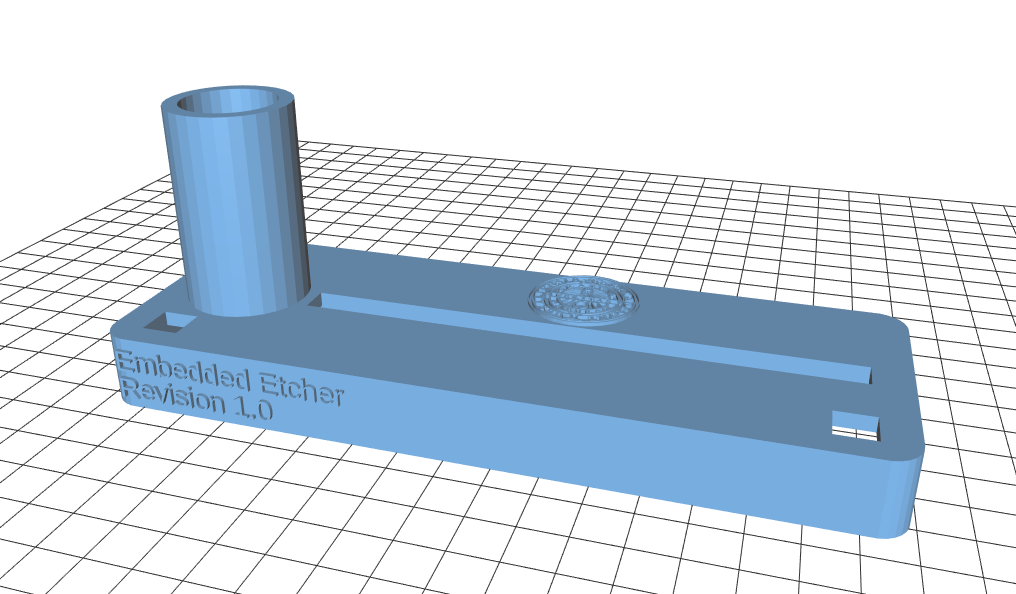
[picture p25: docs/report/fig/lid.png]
   
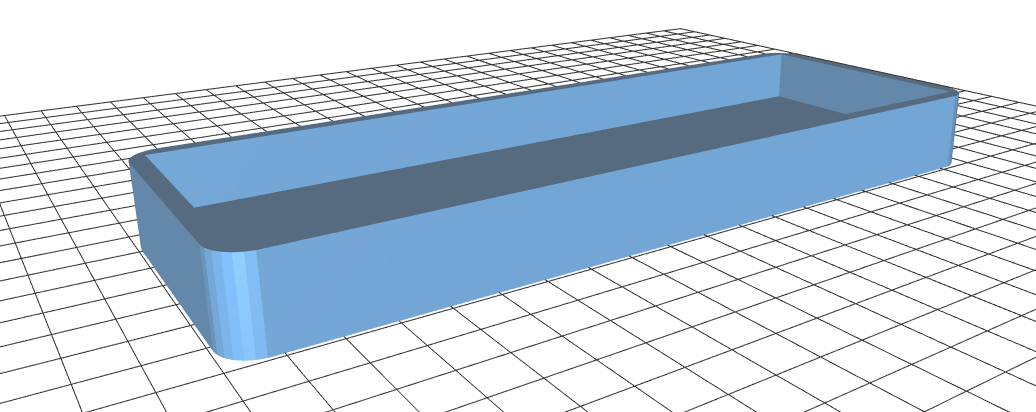
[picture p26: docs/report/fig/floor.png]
 
\caption[Lid and floor of the etching tank.]{Lid and floor of the etching tank.}   
\label{fig:lidFloor} 
\end{figure}

% \begin{figure}[H]
% \centering  
% \includegraphics[width=0.6\textwidth]{./fig/floor}   
% \caption[Floor of the etching tank.]{Floor of the etching tank.}   
% \label{fig:floor} 
% \end{figure} 

\begin{figure}[H]
\centering  
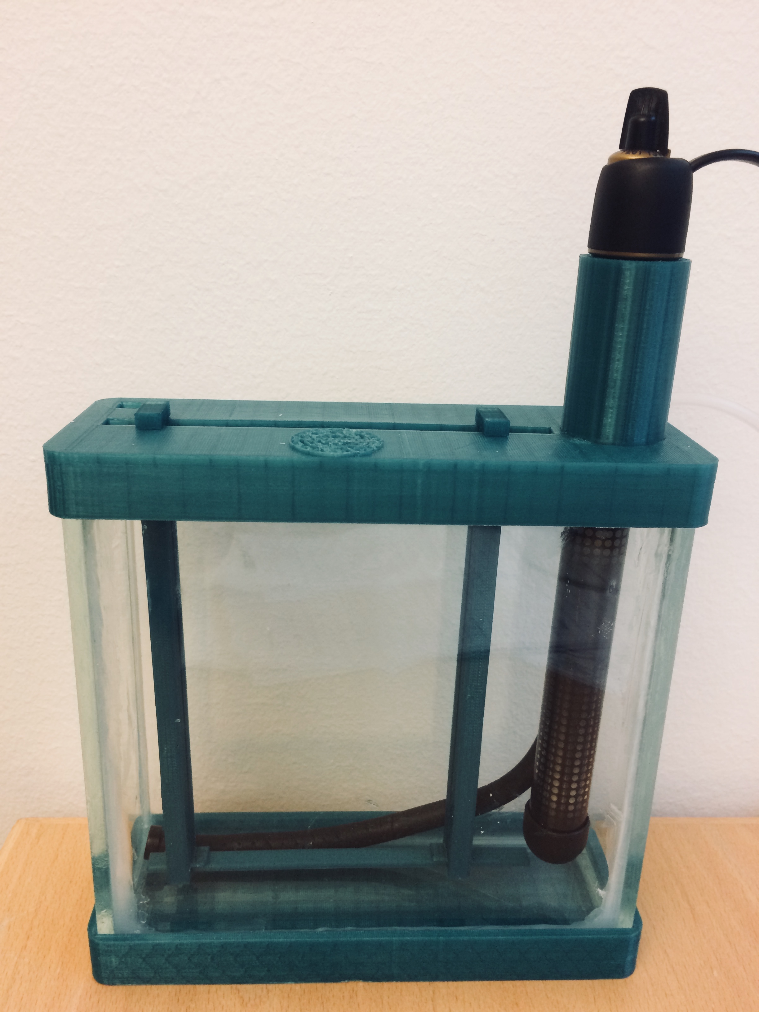
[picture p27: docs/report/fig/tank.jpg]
   
\caption[The etching tank.]{The etching tank.}   
\label{fig:tank} 
\end{figure}

\section{Operating System}
\label{sec:os}

\begin{figure}[H]                                                         
\centering          
   
\caption[Structure of the \gls{OS}]{Structure of the \gls{OS}}   
\label{fig:redhead_os}                                                       
\end{figure}  

In the course of the project a small real-time \gls{OS} has been developed. Fig. \ref{fig:redhead_os} shows how the \gls{OS} is structured. The operating system kernel consists out of a pretty simple scheduler, which is hooked up to the system tick timer, that the \myemph{Cortex-M3} (in the case of the \myemph{STM32F103RB}) provides. Configuring the system tick period is possible. With every system tick the scheduling algorithm is invoked. A state machine is deciding how to handle the system tick. Moreover, the scheduling is based on a binary heap, that contains pointers to the \glspl{TCB} of the tasks, which are supposed to be executed. A task control block is created, when a task is spawned by a programmer with. This works as follows:

\begin{minted}[baselinestretch=1, fontsize=\small, linenos,frame=single,framesep=5pt]{C}
/** Spawn a task.
 *
 * @param ifnc_ptr Pointer to the task function.
 * @param itask_name Internal task name.
 * @param iarguments Enables passing user-defined arguments to the task.
 * @param ipriority A higher value means a higher priority of the task.
 * @param oTaskHandle Pointer to TCB.
 * @retval 1 (task has been spawned) or 0 (FAILED)
 */
uint8_t osTaskCreate(void (*ifnc_ptr)(void*), char* itask_name, void* iarguments, 
	uint8_t ipriority, const osTCB_t* oTaskHandle);
\end{minted}

In general the \gls{OS} interface is frankly speaking inspired by FreeRTOS\texttrademark{}. One can also see, that the scheduling is priority based. The task with the highest priority is always executed as soon as the current task finished its job. Priorities can not be changed on run-time. Of course, as with any real-time \gls{OS} delay functions are available. \myemph{osTaskDelayUntil} is the more important one, as it allows periodic task execution. 

\begin{minted}[baselinestretch=1, fontsize=\small, linenos,frame=single,framesep=5pt]{C}
void task3(void* ptr)
{
	static uint32_t wakeup = 0;
	char* args = (char*)ptr;

	wakeup = osSchedulerGetSysT();
	DEBUG_MSG("%s here!\n\r", args);
	osTaskDelayUntil(wakeup, MS_2_TICKS(300));
}
\end{minted}

As shown in the example above the \gls{TCB} also holds a pointer to data, that can be passed to a task. 
\newpar 
Besides creating a easily understandable real-time \gls{OS} it was intended to provide some smooth infrastructure with it, or rather to equip it with some tools, so that one does not always have to reinvent the wheel, kicking off a new project. Therefore, the \gls{OS} comes with a growing set of accessories as for instance queues (cf. accessories in fig. \ref{fig:redhead_os}). 

\begin{minted}[baselinestretch=1, fontsize=\small, linenos,frame=single,framesep=5pt]{C}
void USART2_IRQHandler(void)
{
	/* USART2 receive buffer contains a char. */
	if(USART_GetITStatus(USART2, USART_IT_RXNE) == SET)
	{
		uint8_t data;
		data = USART_ReceiveData(USART2) & 0xFF;
		if(!osEnqueue(&usart_rx_q, (void*)&data))
			THROW_ERROR(E_USART_RX_BUFFER_OVERLOW);
	}

	/* USART2 transmit buffer empty. */
	if(USART_GetITStatus(USART2, USART_IT_TXE) == SET)
	{
		uint8_t data;
		if(osDequeue(&usart_tx_q, &data))
			USART_SendData(USART2, data);
		else
		{
			/* Nothing to send. Disable interrupt. */
			USART_ITConfig(USART2, USART_IT_TXE, DISABLE);
			tx_overflow = 0;
		}
	}
}
\end{minted}
The code example above shows how the error and the queue accessories can be used to implement the \gls{USART} \gls{IRQ} handler of the \myemph{STM32F103RB} elegantly. The \gls{USART} status register has to be checked for finding out which event triggered the interrupt. Either the transmit buffer is empty again and needs to be fed or the receive buffer contains a char, which needs to be stored somewhere. Both buffers are only as big as 8 bit, so one needs queues, that can be emptied and filled by concurrent processes. The \gls{OS} takes care of that. Also, in this example one can see how an error is passed to the according module in case, the receive buffer overflows. The idea is to have a proper log of what is going on in case the system fails (where did it go wrong and when). Also the sink for error logging can be changed (\gls{EEPROM} / \gls{USART} / screen).
\newpar 
Other accessories are 
\begin{itemize}
\item printf - A light version of \gls{GNU} printf. 
\item semaphores - Different kind of semaphores to get rid of data inconsistency problems that occur with concurrent processes e.g. tasks. 
\item pid - Infrastructure for \gls{PID} controll. 
\item console - A console to command the system and get feedback, similar to a terminal. 
\end{itemize}

The whole \myemph{Doxygen} documentation can be found on \myemph{Github}. 

% \section{Rotary encoder}
% The rotary encoder used for testing and development has a theoretically simple output, however it is of a rather bouncy and thus bad quality, as shown in figure~\ref{fig:re}. Depending on the turning direction either channel A or channel B gets low first and the first one gets high again while the second is still low.
% \begin{figure}[H]
% 	\centering
% 	\includegraphics[width=.8\linewidth]{./fig/re.jpg}
%     \label{fig:re}
% \end{figure}
% Due to many bounces, working with flags, similar to semaphores, is a good option to simply ignore all the bounces. However, one is then restricted to the frequency of calling \texttt{main()}.

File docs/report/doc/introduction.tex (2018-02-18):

%%%%%%%%%%%%%%%%%%%%%%%%%%%%%%%%%%%%%%%%%%%%%%%%%%%%%%%%%%%%%%%%%%%%%%%%%%%%%%%%%%%%%%
%% Author:      Nils Weber and Maximilian Stiefel
%% Date:        23.12.2017
%% University:  Uppsala Universitet
%% Department:  Institutionen för informationsteknologi 
%% Course:      Embedded Control System Project
%% Project:     PRECISELY CONTROLLED DIY ETCHING MACHINE 
%%				FOR USAGE AT HOME AND IN SMALL LABS
%%%%%%%%%%%%%%%%%%%%%%%%%%%%%%%%%%%%%%%%%%%%%%%%%%%%%%%%%%%%%%%%%%%%%%%%%%%%%%%%%%%%%%

\chapter{Introduction} 
\label{chap:introduction} 
At some point in the career an embedded systems engineer needs a quick hardware prototype. One had an idea and wants to try it out. With modern \gls{ECAD} software the \gls{PCB} design is ready within a week or even less. Leading electronic component distributors also guarantee delivery within an acceptable timespan of a few days. However, the preferred \gls{PCB} manufacturer most likely needs a week for the manufacturing and another week for shipping. For this reason, if time is a limited resource, \gls{DIY} etching in the lab can be an option to consider. 

\begin{figure}[H]                                                         
\centering          
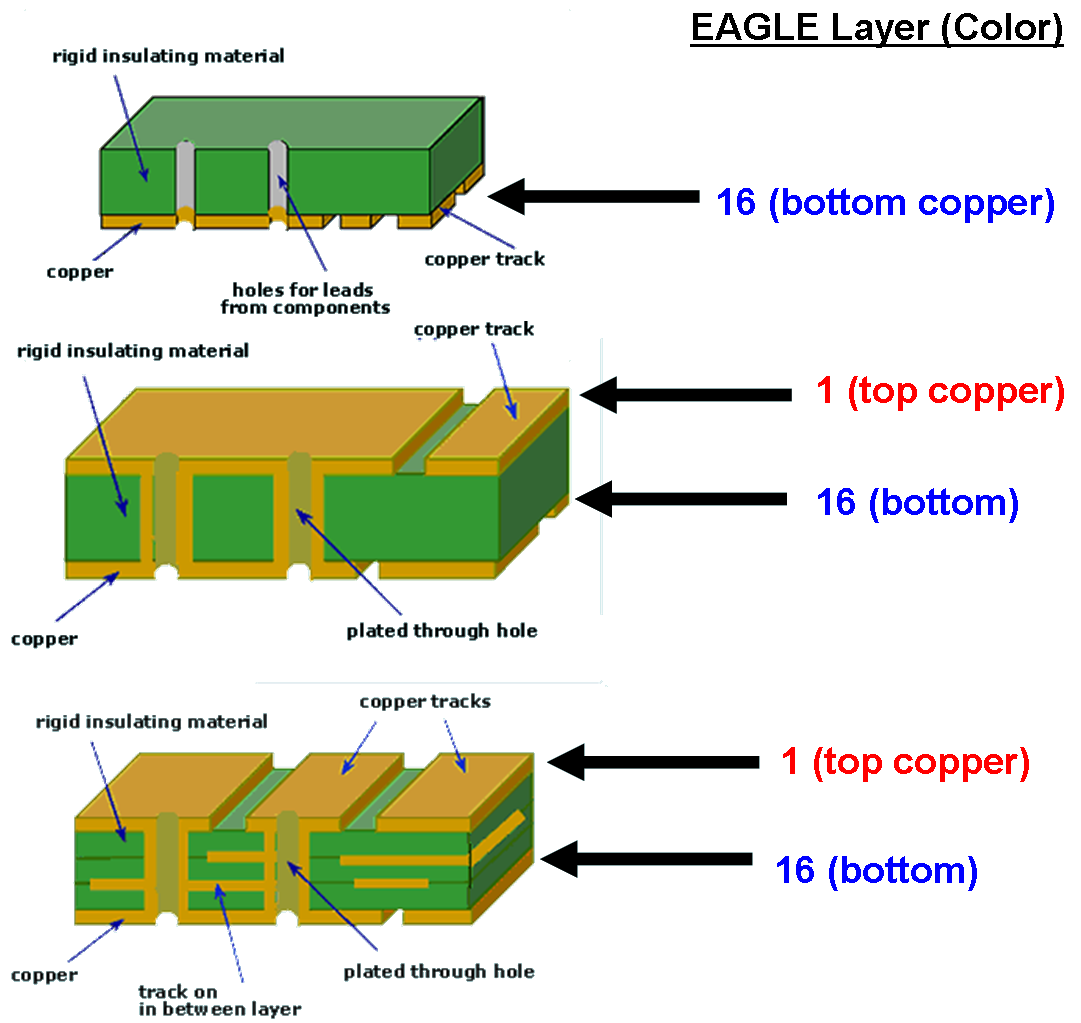
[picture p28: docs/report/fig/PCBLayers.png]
   
\caption[Layered structure of \glspl{PCB}.]{Layered structure of \glspl{PCB}. Top: 1 layer. Middle: 2 layers. Bottom: 4 layers. Source: \cite{online:pcblayers}}   
\label{fig:pcblayers}                                                       
\end{figure}  

A \gls{PCB} basically consists out of copper layers, substrate layers and vias to interconnect different layers (cf. fig. \ref{fig:pcblayers}). There are three different kind of vias in modern electronics:
\begin{enumerate}
\item Through-hole vias as one can see in fig. \ref{fig:pcblayers}
\item Blind vias, which only connect an outer layer to one (or multiple) inner layers
\item Buried vias, which connect two copper layers inside
\end{enumerate}
Blind and buried vias can be implemented as micro vias, which means nothing, but that they are very small, because a laser is used to melt two layers together in a tiny (\ensuremath{<} \SI{0.1}{\milli\metre}) circular area. Conventional \gls{DIY} etching techniques only support the first option. The other two options are usually nowadays still more expensive than normal through-hole vias, which have been around for quite some time already.  Without reservations, using a \gls{DIY} approach, \glspl{PCB} with a complexity of two layers can be crafted nowadays. The basic idea of \gls{DIY} \gls{PCB} crafting is to remove the copper from a blank in certain areas to obtain the desired layout. Distributors nowadays offer blanks with one or two layers and substrate (with a thickness of usually \SI{1.6}{\milli\metre}). Most common is the format \SI{100}{\milli\metre} x \SI{160}{\milli\metre} (\myemph{Eurocard}). Taking away the copper can be achieved mechanically and chemically, whereas this work is about the latter.  
\newpar
\gls{DIY} etching is usually done in either of two ways: 
\begin{enumerate}
\item The toner transfer method: The layout is printed on glossy or transparent paper and the toner is transfered with heat to the blank copper board (cf. \cite{online:instructtoner}). There are several severe disadvantages with this method e.g. that it is hard to align the masks for a \gls{PCB} with two layers.  
\item The photoresist method: Photoresist is used to cover the copper completely and then a \gls{UV} lamp in combination with a mask printed on transparency is leveraged to destroy the photoresist, where it is not covered by the black color on the transparency (cf. \cite{online:instructphoto}). The cracked photoresist, which is damaged by \gls{UV} light can then be washed away with sodium hydroxid (NaOH). 
\end{enumerate}
In both cases an etching bath is necessary to etch away the unprotected copper. Popular chemicals to achieve the copper removal are iron(III) chloride ($\text{FeCl}_3$) and sodium persulfate ($\text{Na}_2\text{S}_2\text{O}_8$).
\newpar
Sodium persulfate gives better results i.e. better or finer contours. Moreover, the sodium persulfate etching liquid is transparent blue unlike the liquid with iron(III) chloride, which is brown and non-transparent. Solving sodium persulfate in water results in
\begin{center}
	\ch{Na2S2O8_{(s)} -> 2 Na^{+}_{(aq)} + S2O8^{2-}_{(aq)}}.
\end{center}
In the etching process elemental copper is oxidated to copper ions, which are then a part of the etching liquid. 
\begin{center}
	\ch{S2O8^{2-}_{(aq)} + Cu_{(s)} -> 2 SO4^{2-}_{(aq)} + Cu^{2+}_{(aq)}}
\end{center}
Special care needs to be taken of the etching liquid afterwards. Copper ions are toxic for all kind of organisms. The last step of \gls{PCB} crafting is the drilling. It can be challenging especially if one uses small via sizes (down to \SI{0.2}{\milli\metre} is not uncommon). One also has to find solution or rather keep in mind, that a via is supposed to interconnect different \gls{PCB} layers, which is hard to achieve creating \gls{PCB} in a \gls{DIY} manner as one somehow has to plate the inside of the cylindric via drill hole with copper in order to create a genuine via.   
% Write what we opt to achieve with this project.
\newpar 
The goal of this project is to develop cheap and easy-to-use etching equipment for the photoresist method. It shall be very easy for engineers to replicate the equipment and also to even tailor it. All the design files shall be open and available on the net. 
\newpar
In principle, what is necessary to start crafting prototypes, is an etching tank and a \gls{UV} light source. Both are subject to what this project opts to achieve as a result.   
\newpar 
The whole project is pushed regularly on \myemph{Github}: \href{https://github.com/m3x1m0m/EmbeddedEtcher}{https://github.com/m3x1m0m/EmbeddedEtcher}

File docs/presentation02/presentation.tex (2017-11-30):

\documentclass[apectratio=169]{beamer}
\usetheme{metropolis}           % Use metropolis theme
% For PDFs
\usepackage{pdfpages}
\usepackage{minted}
\usepackage{tabularx}
\title{DIY Etching Machine}
\subtitle{State of the Art (Papers) and Market Analysis}
\date{\today}
\author{Nils Weber and Maximilian Stiefel}
\institute{Uppsala University}
\begin{document}
  \maketitle

\begin{frame}{Table Of Contents}
  \setbeamertemplate{section in toc}[sections numbered]
  \tableofcontents[hideallsubsections]
\end{frame}

\section{Papers}

\begin{frame}{A buck converter controller design in an electronic drive for LED lighting applications [Iturriaga-Medina et al., 2015]}
  \begin{figure}
    \centering
    
    \caption{Bucket converters are very common in power electronics.}
  \end{figure}	
\end{frame}

\begin{frame}{High-Efficiency Resonant LED Backlight Driver with Passive Current Balancing and Dimming [Xueshan Liu et al., 2017]}
  \begin{figure}
    \centering
    
    \caption{A bit more complex bucket converter.}
  \end{figure}	
\end{frame}

\begin{frame}{Circuit I designed}  
\begin{figure}
    \centering
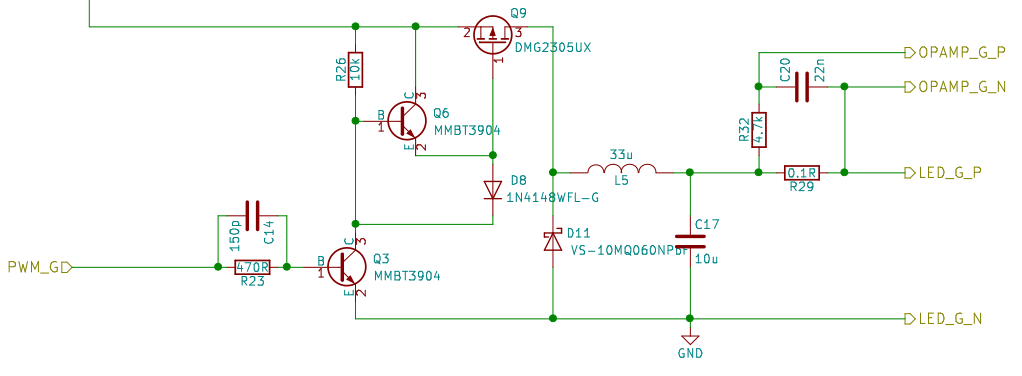
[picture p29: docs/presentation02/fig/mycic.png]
    
    \caption{Quick gate charging bucket converter.}
  \end{figure}	
\end{frame}

\begin{frame}{THE PRINCIPLE OF REVERSED LAG APPLIED TO ON-OFF TEMPERATURE
CONTROL [H. SUTCLIFFE, 1960] (1)}
  \begin{figure}
    \centering
    
    \caption{System overview of two-point control.}
  \end{figure}	
\end{frame}

\begin{frame}{THE PRINCIPLE OF REVERSED LAG APPLIED TO ON-OFF TEMPERATURE
CONTROL [H. SUTCLIFFE, 1960] (2)}
  \begin{figure}
    \centering
    
    \caption{Low-pass behaviour of fluid being excited with a rectangular signal.}
  \end{figure}	
\end{frame}

\section{Market Analysis}

\begin{frame}{Target Group}
  \begin{itemize}
    \item<1-> Hackers
    \item<2-> Researchers, that want a quick prototype
    \item<3-> Engineers, that have no time to wait for China
    \item<4-> People, that watch videos like \href{https://www.youtube.com/watch?v=Hsw3lOnHaas}{this}

  \end{itemize}
 \end{frame}

\begin{frame}{Reichelt Elektronik}
  \centering
  \Huge www.reichelt.de
\end{frame}

\begin{frame}{Example of a modern Etching Machine from Reichelt}
\begin{figure}
    \centering
    
    \caption{Price: 130 EUR. Needed Acid Volume: 1.75 l. Max. PCB Size: 235 mm x 170 mm. Heating Power: 100 W.}
  \end{figure}	
\end{frame}

\begin{frame}{Example of a modern UV Light from Reichelt}
\begin{figure}
    \centering
    
    \caption{Price: 220 EUR. Max. PCB Size: 160 mm x 250 mm. Technology: Fluorescent Tubes (4 x 8 W). Weight: 4 kg.}
  \end{figure}	
\end{frame}

\begin{frame}{Our Goal}
  \begin{itemize}
    \item<1-> Build this equipment at home 
    \item<2-> Try to be cheaper and better
    \item<3> Provide a tutorial on how to build this equipment yourself
  \end{itemize}
\end{frame}

\begin{frame}[standout]
  Happy Coding :) 
\end{frame}

\end{document}

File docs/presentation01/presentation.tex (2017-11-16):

\documentclass[apectratio=169]{beamer}
\usetheme{metropolis}           % Use metropolis theme
% For PDFs
\usepackage{pdfpages}
\usepackage{minted}
\usepackage{tabularx}
\title{Embedded Control Project}
\subtitle{Precisely Controlled DIY Etching Machine For Usage at Home and in Small Labs}
\date{\today}
\author{Nils Weber and Maximilian Stiefel}
\institute{Uppsala University}
\begin{document}
  \maketitle

\begin{frame}{Table Of Contents}
  \setbeamertemplate{section in toc}[sections numbered]
  \tableofcontents[hideallsubsections]
\end{frame}
\section{System Requirements}
  	\begin{frame}{What do we want to achieve?}
		\begin{itemize}
			\item<1-> UV light with 256 LEDs (approx. 30 W)
			\item<2-> Heater for Etching bath
			\item<3-> Neat user interface (rotary knobs, tactile switches and OLED)
			\item<4-> Smart, small, intuitive to use
		\end{itemize}
  	\end{frame}
 \begin{frame}{System Overview}
 \begin{figure}
  
 \end{figure}
 \end{frame}
 \section{State of the Art}
  	\begin{frame}{State of the Art}
		\begin{itemize}
			\item<1-> ARM-based 32 bit processor
			\item<2-> Self-designed current source
			\item<3-> SW-based controllers for aging effects compensation
			\item<4-> SW-based controllers for temperature regulation
		\end{itemize}
  	\end{frame}	
  \begin{frame}[standout]
	Happy Coding :) 
  \end{frame}
\end{document}

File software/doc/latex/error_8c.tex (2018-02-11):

\hypertarget{error_8c}{}\section{os/error.c File Reference}
\label{error_8c}\index{os/error.\+c@{os/error.\+c}}
{\ttfamily \#include $<$stdio.\+h$>$}\newline
{\ttfamily \#include $<$string.\+h$>$}\newline
{\ttfamily \#include $<$stdint.\+h$>$}\newline
{\ttfamily \#include \char`\"{}error.\+h\char`\"{}}\newline
{\ttfamily \#include \char`\"{}helpers.\+h\char`\"{}}\newline
{\ttfamily \#include \char`\"{}printf.\+h\char`\"{}}\newline
{\ttfamily \#include \char`\"{}ossettings.\+h\char`\"{}}\newline
Include dependency graph for error.\+c\+:\nopagebreak
\begin{figure}[H]
\begin{center}
\leavevmode

\end{center}
\end{figure}
\subsection*{Functions}
\begin{DoxyCompactItemize}
\item 
uint8\+\_\+t \hyperlink{error_8c_af770cfb23cba6e7aa7c69aad1bbf968c}{os\+Explain\+Error} (const char $\ast$ifile, const uint8\+\_\+t iline, const \hyperlink{ostypes_8h_acd9f76a1fbd8bc9084ff34add637094f}{os\+Error\+\_\+t} ierror, char $\ast$iomessage)
\item 
uint8\+\_\+t \hyperlink{error_8c_a540c46d0a32421cad29354147a02c4ea}{os\+Print\+Error} (const char $\ast$ifile, const int iline, const \hyperlink{ostypes_8h_acd9f76a1fbd8bc9084ff34add637094f}{os\+Error\+\_\+t} ierror)
\item 
uint8\+\_\+t \hyperlink{error_8c_a29238a23e284dd0a6278434447be4682}{os\+Explain\+Warning} (const char $\ast$ifile, const uint8\+\_\+t iline, const \hyperlink{ostypes_8h_a5c976ef3f21f800d03382e5cc640c362}{os\+Warning\+\_\+t} ierror, char $\ast$iomessage)
\item 
uint8\+\_\+t \hyperlink{error_8c_adeb03b63a59cac38dbdc0e3963d9d479}{os\+Print\+Warning} (const char $\ast$ifile, const int iline, const \hyperlink{ostypes_8h_a5c976ef3f21f800d03382e5cc640c362}{os\+Warning\+\_\+t} iwarning)
\end{DoxyCompactItemize}

\subsection{Function Documentation}
\mbox{\Hypertarget{error_8c_af770cfb23cba6e7aa7c69aad1bbf968c}\label{error_8c_af770cfb23cba6e7aa7c69aad1bbf968c}} 
\index{error.\+c@{error.\+c}!os\+Explain\+Error@{os\+Explain\+Error}}
\index{os\+Explain\+Error@{os\+Explain\+Error}!error.\+c@{error.\+c}}
\subsubsection{\texorpdfstring{os\+Explain\+Error()}{osExplainError()}}
{\footnotesize\ttfamily uint8\+\_\+t os\+Explain\+Error (\begin{DoxyParamCaption}\item[{const char $\ast$}]{ifile,  }\item[{const uint8\+\_\+t}]{iline,  }\item[{const \hyperlink{ostypes_8h_acd9f76a1fbd8bc9084ff34add637094f}{os\+Error\+\_\+t}}]{ierror,  }\item[{char $\ast$}]{iomessage }\end{DoxyParamCaption})}

Creating a error message string from inter alia an error code.

\begin{DoxyParams}{Parameters}
{\em ifile} & Filename where error occurs. \\
\hline
{\em iline} & Line where error occurs. \\
\hline
{\em ierror} & Error code. \\
\hline
{\em message} & Message related to the error. \\
\hline
\end{DoxyParams}

\begin{DoxyRetVals}{Return values}
{\em 1} & (S\+U\+C\+C\+E\+SS) or 0 (F\+A\+I\+L\+U\+RE). \\
\hline
\end{DoxyRetVals}
\mbox{\Hypertarget{error_8c_a29238a23e284dd0a6278434447be4682}\label{error_8c_a29238a23e284dd0a6278434447be4682}} 
\index{error.\+c@{error.\+c}!os\+Explain\+Warning@{os\+Explain\+Warning}}
\index{os\+Explain\+Warning@{os\+Explain\+Warning}!error.\+c@{error.\+c}}
\subsubsection{\texorpdfstring{os\+Explain\+Warning()}{osExplainWarning()}}
{\footnotesize\ttfamily uint8\+\_\+t os\+Explain\+Warning (\begin{DoxyParamCaption}\item[{const char $\ast$}]{ifile,  }\item[{const uint8\+\_\+t}]{iline,  }\item[{const \hyperlink{ostypes_8h_a5c976ef3f21f800d03382e5cc640c362}{os\+Warning\+\_\+t}}]{ierror,  }\item[{char $\ast$}]{iomessage }\end{DoxyParamCaption})}

Creating a warning message string from inter alia a warning code.

\begin{DoxyParams}{Parameters}
{\em ifile} & Filename where warning occurs. \\
\hline
{\em iline} & Line where warning occurs. \\
\hline
{\em ierror} & Warning code. \\
\hline
{\em message} & Message related to the warning. \\
\hline
\end{DoxyParams}

\begin{DoxyRetVals}{Return values}
{\em 1} & (S\+U\+C\+C\+E\+SS) or 0 (F\+A\+I\+L\+U\+RE). \\
\hline
\end{DoxyRetVals}
\mbox{\Hypertarget{error_8c_a540c46d0a32421cad29354147a02c4ea}\label{error_8c_a540c46d0a32421cad29354147a02c4ea}} 
\index{error.\+c@{error.\+c}!os\+Print\+Error@{os\+Print\+Error}}
\index{os\+Print\+Error@{os\+Print\+Error}!error.\+c@{error.\+c}}
\subsubsection{\texorpdfstring{os\+Print\+Error()}{osPrintError()}}
{\footnotesize\ttfamily uint8\+\_\+t os\+Print\+Error (\begin{DoxyParamCaption}\item[{const char $\ast$}]{ifile,  }\item[{const int}]{iline,  }\item[{const \hyperlink{ostypes_8h_acd9f76a1fbd8bc9084ff34add637094f}{os\+Error\+\_\+t}}]{ierror }\end{DoxyParamCaption})}

Print error. This is where the error output can be redirected (later).

\begin{DoxyParams}{Parameters}
{\em ifile} & Filename where error occurs. \\
\hline
{\em iline} & Line where error occurs. \\
\hline
{\em ierror} & Error code. \\
\hline
\end{DoxyParams}

\begin{DoxyRetVals}{Return values}
{\em 1} & (S\+U\+C\+C\+E\+SS) or 0 (F\+A\+I\+L\+U\+RE). \\
\hline
\end{DoxyRetVals}
\mbox{\Hypertarget{error_8c_adeb03b63a59cac38dbdc0e3963d9d479}\label{error_8c_adeb03b63a59cac38dbdc0e3963d9d479}} 
\index{error.\+c@{error.\+c}!os\+Print\+Warning@{os\+Print\+Warning}}
\index{os\+Print\+Warning@{os\+Print\+Warning}!error.\+c@{error.\+c}}
\subsubsection{\texorpdfstring{os\+Print\+Warning()}{osPrintWarning()}}
{\footnotesize\ttfamily uint8\+\_\+t os\+Print\+Warning (\begin{DoxyParamCaption}\item[{const char $\ast$}]{ifile,  }\item[{const int}]{iline,  }\item[{const \hyperlink{ostypes_8h_a5c976ef3f21f800d03382e5cc640c362}{os\+Warning\+\_\+t}}]{ierror }\end{DoxyParamCaption})}

Print warning. This is where the warning output can be redirected (later).

\begin{DoxyParams}{Parameters}
{\em ifile} & Filename where warning occurs. \\
\hline
{\em iline} & Line where warning occurs. \\
\hline
{\em ierror} & Warning code. \\
\hline
\end{DoxyParams}

\begin{DoxyRetVals}{Return values}
{\em 1} & (S\+U\+C\+C\+E\+SS) or 0 (F\+A\+I\+L\+U\+RE). \\
\hline
\end{DoxyRetVals}

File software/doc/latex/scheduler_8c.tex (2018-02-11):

\hypertarget{scheduler_8c}{}\section{os/scheduler.c File Reference}
\label{scheduler_8c}\index{os/scheduler.\+c@{os/scheduler.\+c}}
{\ttfamily \#include $<$stdlib.\+h$>$}\newline
{\ttfamily \#include $<$stdio.\+h$>$}\newline
{\ttfamily \#include $<$stdint.\+h$>$}\newline
{\ttfamily \#include $<$string.\+h$>$}\newline
{\ttfamily \#include \char`\"{}scheduler.\+h\char`\"{}}\newline
{\ttfamily \#include \char`\"{}error.\+h\char`\"{}}\newline
{\ttfamily \#include \char`\"{}heap.\+h\char`\"{}}\newline
{\ttfamily \#include \char`\"{}printf.\+h\char`\"{}}\newline
{\ttfamily \#include \char`\"{}ossettings.\+h\char`\"{}}\newline
{\ttfamily \#include \char`\"{}../platform/system\+\_\+timer.\+h\char`\"{}}\newline
Include dependency graph for scheduler.\+c\+:\nopagebreak
\begin{figure}[H]
\begin{center}
\leavevmode

\end{center}
\end{figure}
\subsection*{Functions}
\begin{DoxyCompactItemize}
\item 
uint32\+\_\+t \hyperlink{scheduler_8c_ac59673f226b3291f835a0faf010ad409}{os\+Scheduler\+Get\+SysT} (void)
\item 
uint8\+\_\+t \hyperlink{scheduler_8c_a76739fd1872ff1f867ea41e853131a21}{os\+Task\+Create} (void($\ast$ifnc\+\_\+ptr)(void $\ast$), char $\ast$itask\+\_\+name, void $\ast$iarguments, uint8\+\_\+t ipriority, const \hyperlink{structos_t_c_b__t}{os\+T\+C\+B\+\_\+t} $\ast$o\+Task\+Handle)
\item 
void \hyperlink{scheduler_8c_a790ca9c0d2362305790eb3c4002e3da9}{os\+Task\+Delete} (\hyperlink{structos_t_c_b__t}{os\+T\+C\+B\+\_\+t} $\ast$iotask)
\item 
void \hyperlink{scheduler_8c_ae1e7565174265c0107749d7cdf486c01}{os\+Task\+Delay} (uint8\+\_\+t idelay)
\item 
void \hyperlink{scheduler_8c_ae4c7af5e41838a9299b00d455fb8f454}{os\+Task\+Delay\+Until} (uint32\+\_\+t iwakeup\+\_\+time, uint8\+\_\+t idelay)
\item 
void \hyperlink{scheduler_8c_ada28e10d8b44223004cab16b201df2d7}{os\+Run\+Scheduler} (void)
\item 
void \hyperlink{scheduler_8c_acd27cd0dcb4e193125968decdd238ff9}{os\+Print\+Task} (uint8\+\_\+t iindex)
\item 
void \hyperlink{scheduler_8c_ad4967a4ccbd9e8901a1d79a9ee3ca79b}{os\+Print\+All\+Tasks} (void)
\end{DoxyCompactItemize}

\subsection{Function Documentation}
\mbox{\Hypertarget{scheduler_8c_ad4967a4ccbd9e8901a1d79a9ee3ca79b}\label{scheduler_8c_ad4967a4ccbd9e8901a1d79a9ee3ca79b}} 
\index{scheduler.\+c@{scheduler.\+c}!os\+Print\+All\+Tasks@{os\+Print\+All\+Tasks}}
\index{os\+Print\+All\+Tasks@{os\+Print\+All\+Tasks}!scheduler.\+c@{scheduler.\+c}}
\subsubsection{\texorpdfstring{os\+Print\+All\+Tasks()}{osPrintAllTasks()}}
{\footnotesize\ttfamily void os\+Print\+All\+Tasks (\begin{DoxyParamCaption}\item[{void}]{ }\end{DoxyParamCaption})}

Print all information about all tasks. \mbox{\Hypertarget{scheduler_8c_acd27cd0dcb4e193125968decdd238ff9}\label{scheduler_8c_acd27cd0dcb4e193125968decdd238ff9}} 
\index{scheduler.\+c@{scheduler.\+c}!os\+Print\+Task@{os\+Print\+Task}}
\index{os\+Print\+Task@{os\+Print\+Task}!scheduler.\+c@{scheduler.\+c}}
\subsubsection{\texorpdfstring{os\+Print\+Task()}{osPrintTask()}}
{\footnotesize\ttfamily void os\+Print\+Task (\begin{DoxyParamCaption}\item[{uint8\+\_\+t}]{iindex }\end{DoxyParamCaption})}

Print all information about one task.

\begin{DoxyParams}{Parameters}
{\em iindex} & Index in the T\+CB array. \\
\hline
\end{DoxyParams}
\mbox{\Hypertarget{scheduler_8c_ada28e10d8b44223004cab16b201df2d7}\label{scheduler_8c_ada28e10d8b44223004cab16b201df2d7}} 
\index{scheduler.\+c@{scheduler.\+c}!os\+Run\+Scheduler@{os\+Run\+Scheduler}}
\index{os\+Run\+Scheduler@{os\+Run\+Scheduler}!scheduler.\+c@{scheduler.\+c}}
\subsubsection{\texorpdfstring{os\+Run\+Scheduler()}{osRunScheduler()}}
{\footnotesize\ttfamily void os\+Run\+Scheduler (\begin{DoxyParamCaption}\item[{void}]{ }\end{DoxyParamCaption})}

System core. Scheduler needs to be executed by a timer interrupt. \mbox{\Hypertarget{scheduler_8c_ac59673f226b3291f835a0faf010ad409}\label{scheduler_8c_ac59673f226b3291f835a0faf010ad409}} 
\index{scheduler.\+c@{scheduler.\+c}!os\+Scheduler\+Get\+SysT@{os\+Scheduler\+Get\+SysT}}
\index{os\+Scheduler\+Get\+SysT@{os\+Scheduler\+Get\+SysT}!scheduler.\+c@{scheduler.\+c}}
\subsubsection{\texorpdfstring{os\+Scheduler\+Get\+Sys\+T()}{osSchedulerGetSysT()}}
{\footnotesize\ttfamily uint32\+\_\+t os\+Scheduler\+Get\+SysT (\begin{DoxyParamCaption}\item[{void}]{ }\end{DoxyParamCaption})}

Get the system time.

\begin{DoxyRetVals}{Return values}
{\em Gives} & back the number of ticks since system has been initialized. \\
\hline
\end{DoxyRetVals}
\mbox{\Hypertarget{scheduler_8c_a76739fd1872ff1f867ea41e853131a21}\label{scheduler_8c_a76739fd1872ff1f867ea41e853131a21}} 
\index{scheduler.\+c@{scheduler.\+c}!os\+Task\+Create@{os\+Task\+Create}}
\index{os\+Task\+Create@{os\+Task\+Create}!scheduler.\+c@{scheduler.\+c}}
\subsubsection{\texorpdfstring{os\+Task\+Create()}{osTaskCreate()}}
{\footnotesize\ttfamily uint8\+\_\+t os\+Task\+Create (\begin{DoxyParamCaption}\item[{void($\ast$)(void $\ast$)}]{ifnc\+\_\+ptr,  }\item[{char $\ast$}]{itask\+\_\+name,  }\item[{void $\ast$}]{iarguments,  }\item[{uint8\+\_\+t}]{ipriority,  }\item[{const \hyperlink{structos_t_c_b__t}{os\+T\+C\+B\+\_\+t} $\ast$}]{o\+Task\+Handle }\end{DoxyParamCaption})}

Spawn a task.

\begin{DoxyParams}{Parameters}
{\em ifnc\+\_\+ptr} & Pointer to the task function. \\
\hline
{\em itask\+\_\+name} & Internal task name. \\
\hline
{\em iarguments} & Enables passing user-\/defined arguments to the task. \\
\hline
{\em ipriority} & A higher value means a higher priority of the task. \\
\hline
{\em o\+Task\+Handle} & Pointer to T\+CB. \\
\hline
\end{DoxyParams}

\begin{DoxyRetVals}{Return values}
{\em 1} & (task has been spawned) or 0 (F\+A\+I\+L\+ED) \\
\hline
\end{DoxyRetVals}
\mbox{\Hypertarget{scheduler_8c_ae1e7565174265c0107749d7cdf486c01}\label{scheduler_8c_ae1e7565174265c0107749d7cdf486c01}} 
\index{scheduler.\+c@{scheduler.\+c}!os\+Task\+Delay@{os\+Task\+Delay}}
\index{os\+Task\+Delay@{os\+Task\+Delay}!scheduler.\+c@{scheduler.\+c}}
\subsubsection{\texorpdfstring{os\+Task\+Delay()}{osTaskDelay()}}
{\footnotesize\ttfamily void os\+Task\+Delay (\begin{DoxyParamCaption}\item[{uint8\+\_\+t}]{idelay }\end{DoxyParamCaption})}

Delay function. DO N\+OT U\+SE F\+OR P\+E\+R\+I\+O\+D\+IC T\+A\+S\+K\+S!

\begin{DoxyParams}{Parameters}
{\em idelay} & Delay in system ticks. \\
\hline
\end{DoxyParams}
\mbox{\Hypertarget{scheduler_8c_ae4c7af5e41838a9299b00d455fb8f454}\label{scheduler_8c_ae4c7af5e41838a9299b00d455fb8f454}} 
\index{scheduler.\+c@{scheduler.\+c}!os\+Task\+Delay\+Until@{os\+Task\+Delay\+Until}}
\index{os\+Task\+Delay\+Until@{os\+Task\+Delay\+Until}!scheduler.\+c@{scheduler.\+c}}
\subsubsection{\texorpdfstring{os\+Task\+Delay\+Until()}{osTaskDelayUntil()}}
{\footnotesize\ttfamily void os\+Task\+Delay\+Until (\begin{DoxyParamCaption}\item[{uint32\+\_\+t}]{iwakeup\+\_\+time,  }\item[{uint8\+\_\+t}]{idelay }\end{DoxyParamCaption})}

Delay until function. DO U\+SE F\+OR P\+E\+R\+I\+O\+D\+IC T\+A\+S\+K\+S!

\begin{DoxyParams}{Parameters}
{\em iwakeup\+\_\+time} & Time when the task execution started. \\
\hline
{\em idelay} & Number of system ticks until the task shall be executed again. \\
\hline
\end{DoxyParams}
\mbox{\Hypertarget{scheduler_8c_a790ca9c0d2362305790eb3c4002e3da9}\label{scheduler_8c_a790ca9c0d2362305790eb3c4002e3da9}} 
\index{scheduler.\+c@{scheduler.\+c}!os\+Task\+Delete@{os\+Task\+Delete}}
\index{os\+Task\+Delete@{os\+Task\+Delete}!scheduler.\+c@{scheduler.\+c}}
\subsubsection{\texorpdfstring{os\+Task\+Delete()}{osTaskDelete()}}
{\footnotesize\ttfamily void os\+Task\+Delete (\begin{DoxyParamCaption}\item[{\hyperlink{structos_t_c_b__t}{os\+T\+C\+B\+\_\+t} $\ast$}]{iotask }\end{DoxyParamCaption})}

Simply delete task by setting the function pointer to N\+U\+LL.

\begin{DoxyParams}{Parameters}
{\em iotask} & Pointer to T\+CB. \\
\hline
\end{DoxyParams}

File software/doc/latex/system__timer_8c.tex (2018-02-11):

\hypertarget{system__timer_8c}{}\section{platform/system\+\_\+timer.c File Reference}
\label{system__timer_8c}\index{platform/system\+\_\+timer.\+c@{platform/system\+\_\+timer.\+c}}
{\ttfamily \#include $<$stm32f10x.\+h$>$}\newline
{\ttfamily \#include $<$stm32f10x\+\_\+flash.\+h$>$}\newline
{\ttfamily \#include $<$stm32f10x\+\_\+rcc.\+h$>$}\newline
{\ttfamily \#include \char`\"{}../os/scheduler.\+h\char`\"{}}\newline
{\ttfamily \#include \char`\"{}../os/ossettings.\+h\char`\"{}}\newline
Include dependency graph for system\+\_\+timer.\+c\+:\nopagebreak
\begin{figure}[H]
\begin{center}
\leavevmode

\end{center}
\end{figure}
\subsection*{Functions}
\begin{DoxyCompactItemize}
\item 
void \hyperlink{system__timer_8c_aa2e1abc835e556904f718ede78c1df6f}{init\+Alive\+L\+ED} (void)
\item 
void \hyperlink{system__timer_8c_af9e6109b87e10db9303be55cffb97498}{toggle\+Alive\+L\+ED} (void)
\item 
void \hyperlink{system__timer_8c_a2ef37c6b4d5f172facf1a8cef7fcedd5}{init\+Clock} (void)
\item 
void \hyperlink{system__timer_8c_ab5e09814056d617c521549e542639b7e}{Sys\+Tick\+\_\+\+Handler} (void)
\end{DoxyCompactItemize}

\subsection{Function Documentation}
\mbox{\Hypertarget{system__timer_8c_aa2e1abc835e556904f718ede78c1df6f}\label{system__timer_8c_aa2e1abc835e556904f718ede78c1df6f}} 
\index{system\+\_\+timer.\+c@{system\+\_\+timer.\+c}!init\+Alive\+L\+ED@{init\+Alive\+L\+ED}}
\index{init\+Alive\+L\+ED@{init\+Alive\+L\+ED}!system\+\_\+timer.\+c@{system\+\_\+timer.\+c}}
\subsubsection{\texorpdfstring{init\+Alive\+L\+E\+D()}{initAliveLED()}}
{\footnotesize\ttfamily void init\+Alive\+L\+ED (\begin{DoxyParamCaption}\item[{void}]{ }\end{DoxyParamCaption})}

\mbox{\Hypertarget{system__timer_8c_a2ef37c6b4d5f172facf1a8cef7fcedd5}\label{system__timer_8c_a2ef37c6b4d5f172facf1a8cef7fcedd5}} 
\index{system\+\_\+timer.\+c@{system\+\_\+timer.\+c}!init\+Clock@{init\+Clock}}
\index{init\+Clock@{init\+Clock}!system\+\_\+timer.\+c@{system\+\_\+timer.\+c}}
\subsubsection{\texorpdfstring{init\+Clock()}{initClock()}}
{\footnotesize\ttfamily void init\+Clock (\begin{DoxyParamCaption}\item[{void}]{ }\end{DoxyParamCaption})}

\mbox{\Hypertarget{system__timer_8c_ab5e09814056d617c521549e542639b7e}\label{system__timer_8c_ab5e09814056d617c521549e542639b7e}} 
\index{system\+\_\+timer.\+c@{system\+\_\+timer.\+c}!Sys\+Tick\+\_\+\+Handler@{Sys\+Tick\+\_\+\+Handler}}
\index{Sys\+Tick\+\_\+\+Handler@{Sys\+Tick\+\_\+\+Handler}!system\+\_\+timer.\+c@{system\+\_\+timer.\+c}}
\subsubsection{\texorpdfstring{Sys\+Tick\+\_\+\+Handler()}{SysTick\_Handler()}}
{\footnotesize\ttfamily void Sys\+Tick\+\_\+\+Handler (\begin{DoxyParamCaption}\item[{void}]{ }\end{DoxyParamCaption})}

\mbox{\Hypertarget{system__timer_8c_af9e6109b87e10db9303be55cffb97498}\label{system__timer_8c_af9e6109b87e10db9303be55cffb97498}} 
\index{system\+\_\+timer.\+c@{system\+\_\+timer.\+c}!toggle\+Alive\+L\+ED@{toggle\+Alive\+L\+ED}}
\index{toggle\+Alive\+L\+ED@{toggle\+Alive\+L\+ED}!system\+\_\+timer.\+c@{system\+\_\+timer.\+c}}
\subsubsection{\texorpdfstring{toggle\+Alive\+L\+E\+D()}{toggleAliveLED()}}
{\footnotesize\ttfamily void toggle\+Alive\+L\+ED (\begin{DoxyParamCaption}\item[{void}]{ }\end{DoxyParamCaption})}

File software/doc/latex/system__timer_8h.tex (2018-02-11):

\hypertarget{system__timer_8h}{}\section{platform/system\+\_\+timer.h File Reference}
\label{system__timer_8h}\index{platform/system\+\_\+timer.\+h@{platform/system\+\_\+timer.\+h}}
This graph shows which files directly or indirectly include this file\+:\nopagebreak
\begin{figure}[H]
\begin{center}
\leavevmode

\end{center}
\end{figure}
\subsection*{Functions}
\begin{DoxyCompactItemize}
\item 
void \hyperlink{system__timer_8h_aa2e1abc835e556904f718ede78c1df6f}{init\+Alive\+L\+ED} (void)
\item 
void \hyperlink{system__timer_8h_af9e6109b87e10db9303be55cffb97498}{toggle\+Alive\+L\+ED} (void)
\item 
void \hyperlink{system__timer_8h_a2ef37c6b4d5f172facf1a8cef7fcedd5}{init\+Clock} (void)
\end{DoxyCompactItemize}

\subsection{Function Documentation}
\mbox{\Hypertarget{system__timer_8h_aa2e1abc835e556904f718ede78c1df6f}\label{system__timer_8h_aa2e1abc835e556904f718ede78c1df6f}} 
\index{system\+\_\+timer.\+h@{system\+\_\+timer.\+h}!init\+Alive\+L\+ED@{init\+Alive\+L\+ED}}
\index{init\+Alive\+L\+ED@{init\+Alive\+L\+ED}!system\+\_\+timer.\+h@{system\+\_\+timer.\+h}}
\subsubsection{\texorpdfstring{init\+Alive\+L\+E\+D()}{initAliveLED()}}
{\footnotesize\ttfamily void init\+Alive\+L\+ED (\begin{DoxyParamCaption}\item[{void}]{ }\end{DoxyParamCaption})}

\mbox{\Hypertarget{system__timer_8h_a2ef37c6b4d5f172facf1a8cef7fcedd5}\label{system__timer_8h_a2ef37c6b4d5f172facf1a8cef7fcedd5}} 
\index{system\+\_\+timer.\+h@{system\+\_\+timer.\+h}!init\+Clock@{init\+Clock}}
\index{init\+Clock@{init\+Clock}!system\+\_\+timer.\+h@{system\+\_\+timer.\+h}}
\subsubsection{\texorpdfstring{init\+Clock()}{initClock()}}
{\footnotesize\ttfamily void init\+Clock (\begin{DoxyParamCaption}\item[{void}]{ }\end{DoxyParamCaption})}

\mbox{\Hypertarget{system__timer_8h_af9e6109b87e10db9303be55cffb97498}\label{system__timer_8h_af9e6109b87e10db9303be55cffb97498}} 
\index{system\+\_\+timer.\+h@{system\+\_\+timer.\+h}!toggle\+Alive\+L\+ED@{toggle\+Alive\+L\+ED}}
\index{toggle\+Alive\+L\+ED@{toggle\+Alive\+L\+ED}!system\+\_\+timer.\+h@{system\+\_\+timer.\+h}}
\subsubsection{\texorpdfstring{toggle\+Alive\+L\+E\+D()}{toggleAliveLED()}}
{\footnotesize\ttfamily void toggle\+Alive\+L\+ED (\begin{DoxyParamCaption}\item[{void}]{ }\end{DoxyParamCaption})}

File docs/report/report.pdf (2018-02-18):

# Uppsala University

# PRECISELY CONTROLLED DIY ETCHING MACHINE FOR USAGE AT HOME AND IN SMALL LABS

## Project Report

## for the project course of Embedded Control Systems (1RT911) carried out in the autumn term 2017 (HT17)

## Deadline: 2018-01-12 12:00

Student | Student | Supervisor
Nils Weber | Maximilian Stiefel | Alexander Medvedev
(Nilsthorben.Weber.3030@student.uu.se) | (Maximilian.Stiefel.8233@student.uu.se) | (Alexander.Medvedev@it.uu.se)

# Contents

1 Introduction | 1
2 Background and Analysis | 3
3 Design | 9
4 Implementation | 13
5 Evaluation | 24
6 Conclusion and Future Work | 26
A Schematics Extension Board | IV
B Technical drawings of PCB-holder | X

# List of Figures

1.1 Layered structure of Printed Circuit Boards (PCBs) | | 1
2.1 Typcial buck converter as it can be found in a car | | 5
2.2 More complex buck converter for automotive applications with analog control circuit. . . | 6
2.3 Typical linear regulator circuit | | 7
2.4 Waveforms of heating power and temperature of a system with on-off control | | 7
2.5 The control system with unity negative feedback and inertia corrector | | 8
2.6 The control system with proportional and inertia correctors | | 8
3.1 µCwithuserinterf ace, customLEDdriverandfeedbackloop | | 9
3.2 µCwithuserinterf ace, heaterandfeedbackloop | | 10
4.1 UV light system | | 13
4.2 Four layer extension board for the Nucleo-F103RB | | 14
4.3 Layered code structure | | 16
4.4 Wooden box for the Ultraviolet (UV) exposer unit | | 17
4.5 Adapter board for Light Emitting Diode (LED) matrix enables simple plug and play. . . . | 17
4.6 Lid and floor of the etching tank | | 20
4.7 The etching tank | | 20
4.8 Structure of the Operating System (OS) | | 21
B.1 Technical Drawing: Crossbar | | X
B.2 Technical Drawing: Floor | | X
B.3 Technical Drawing: Holder | | XI
B.4 Technical Drawing: Lid | | XI

II

# List of Tables

2.1 Market analysis | | 3
3.1 Design choices for the system: Why has each component been chosen? | | 11
5.1 Status Quo OS | | 24
5.2 Status Quo UV light | | 24
5.3 Status Quo etching bath | | 25

III

# 1 Introduction

At some point in the career an embedded systems engineer needs a quick hardware prototype. One had an idea and wants to try it out. With modern Electronic Computer-Aided Design (ECAD) software the PCB design is ready within a week or even less. Leading electronic component distributors also guarantee delivery within an acceptable timespan of a few days. However, the preferred PCB manufacturer most likely needs a week for the manufacturing and another week for shipping. For this reason, if time is a limited resource, Do It Yourself (DIY) etching in the lab can be an option to consider.


Figure 1.1: Layered structure of PCBs. Top: 1 layer. Middle: 2 layers. Bottom: 4 layers. Source: online:pcblayers

A PCB basically consists out of copper layers, substrate layers and vias to interconnect different layers (cf. fig. 1.1). There are three different kind of vias in modern electronics:

1. Through-hole vias as one can see in fig. 1.1
2. Blind vias, which only connect an outer layer to one (or multiple) inner layers
3. Buried vias, which connect two copper layers inside

Blind and buried vias can be implemented as micro vias, which means nothing, but that they are very small, because a laser is used to melt two layers together in a tiny (< 0.1 mm) circular area. Conventional DIY etching techniques only support the first option. The other two options are usually nowadays still

CHAPTER 1. INTRODUCTION —

more expensive than normal through-hole vias, which have been around for quite some time already. Without reservations, using a DIY approach, PCBs with a complexity of two layers can be crafted nowadays. The basic idea of DIY PCB crafting is to remove the copper from a blank in certain areas to obtain the desired layout. Distributors nowadays offer blanks with one or two layers and substrate (with a thickness of usually 1.6 mm). Most common is the format 100 mm x 160 mm (Eurocard). Taking away the copper can be achieved mechanically and chemically, whereas this work is about the latter.

DIY etching is usually done in either of two ways:

1. The toner transfer method: The layout is printed on glossy or transparent paper and the toner is transfered with heat to the blank copper board (cf. online:instructtoner). There are several severe disadvantages with this method e.g. that it is hard to align the masks for a PCB with two layers.
2. The photoresist method: Photoresist is used to cover the copper completely and then a UV lamp in combination with a mask printed on transparency is leveraged to destroy the photoresist, where it is not covered by the black color on the transparency (cf. online:instructphoto). The cracked photoresist, which is damaged by UV light can then be washed away with sodium hydroxid (NaOH).

In both cases an etching bath is necessary to etch away the unprotected copper. Popular chemicals to achieve the copper removal are iron(III) chloride (FeCl3) and sodium persulfate (Na2S2O8).

Sodium persulfate gives better results i.e. better or finer contours. Moreover, the sodium persulfate etching liquid is transparent blue unlike the liquid with iron(III) chloride, which is brown and nontransparent. Solving sodium persulfate in water results in

Na2S2O8(s) 2 Na ⁺ (aq) + S2O

2–
8(aq).

In the etching process elemental copper is oxidated to copper ions, which are then a part of the etching liquid.

S2O

2–
8(aq) + Cu(s) 2 SO ²⁻ 4(aq) + Cu ²⁺
(aq)

Special care needs to be taken of the etching liquid afterwards. Copper ions are toxic for all kind of organisms. The last step of PCB crafting is the drilling. It can be challenging especially if one uses small via sizes (down to 0.2 mm is not uncommon). One also has to find solution or rather keep in mind, that a via is supposed to interconnect different PCB layers, which is hard to achieve creating PCB in a DIY manner as one somehow has to plate the inside of the cylindric via drill hole with copper in order to create a genuine via.

The goal of this project is to develop cheap and easy-to-use etching equipment for the photoresist method. It shall be very easy for engineers to replicate the equipment and also to even tailor it. All the design files shall be open and available on the net.

In principle, what is necessary to start crafting prototypes, is an etching tank and a UV light source. Both are subject to what this project opts to achieve as a result.

The whole project is pushed regularly on Github: https://github.com/m3x1m0m/EmbeddedEtcher

# 2 Background and Analysis
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

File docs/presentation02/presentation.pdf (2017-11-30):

### DIY Etching Machine

State of the Art (Papers) and Market Analysis

Nils Weber and Maximilian Stiefel

November 29, 2017

Uppsala University

Table Of Contents

1. Papers
2. Market Analysis

### Papers

A buck converter controller design in an electronic drive for LED lighting applications [Iturriaga-Medina et al., 2015]


Figure 1: Bucket converters are very common in power electronics.

High-Efficiency Resonant LED Backlight Driver with Passive Current Balancing and Dimming [Xueshan Liu et al., 2017]


Figure 2: A bit more complex bucket converter.

Circuit I designed


Figure 3: Quick gate charging bucket converter.

THE PRINCIPLE OF REVERSED LAG APPLIED TO ON-OFF TEMPERATURE CONTROL [H. SUTCLIFFE, 1960] (1)


Figure 4: System overview of two-point control.

THE PRINCIPLE OF REVERSED LAG APPLIED TO ON-OFF TEMPERATURE CONTROL [H. SUTCLIFFE, 1960] (2)


Figure 5: Low-pass behaviour of fluid being excited with a rectangular
signal. | 6

### Market Analysis

Target Group

- Hackers

Target Group

- Hackers
- Researchers, that want a quick prototype

Target Group

- Hackers
- Researchers, that want a quick prototype
- Engineers, that have no time to wait for China

Target Group

- Hackers
- Researchers, that want a quick prototype
- Engineers, that have no time to wait for China
- People, that watch videos like this (https://www.youtube.com/watch?v=Hsw3lOnHaas)

Reichelt Elektronik

# www.reichelt.de

Example of a modern Etching Machine from Reichelt


Figure 6: Price: 130 EUR. Needed Acid Volume: 1.75 l. Max. PCB Size: 235 mm x 170 mm. Heating Power: 100 W.

Example of a modern UV Light from Reichelt


Figure 7: Price: 220 EUR. Max. PCB Size: 160 mm x 250 mm. Technology: Fluorescent Tubes (4 x 8 W). Weight: 4 kg.

Our Goal

- Build this equipment at home

Our Goal

- Build this equipment at home
- Try to be cheaper and better

Our Goal

- Build this equipment at home
- Try to be cheaper and better
- Provide a tutorial on how to build this equipment yourself
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

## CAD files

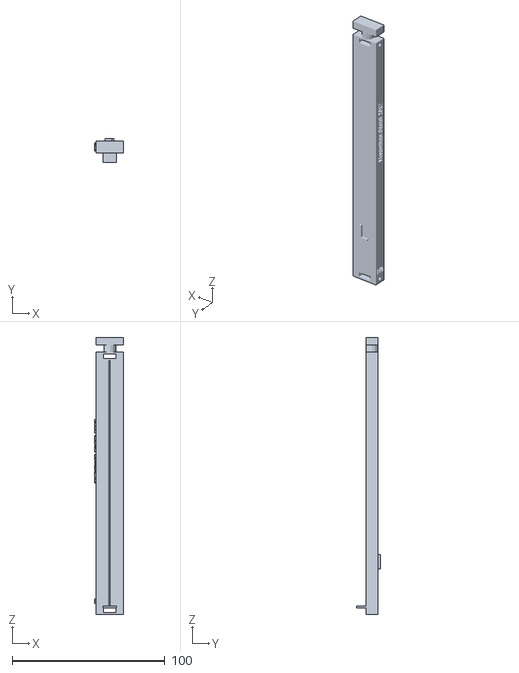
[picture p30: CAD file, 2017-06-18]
cad/output/pcb_holder_holder_l.stl
19.0 x 15.5 x 181.5

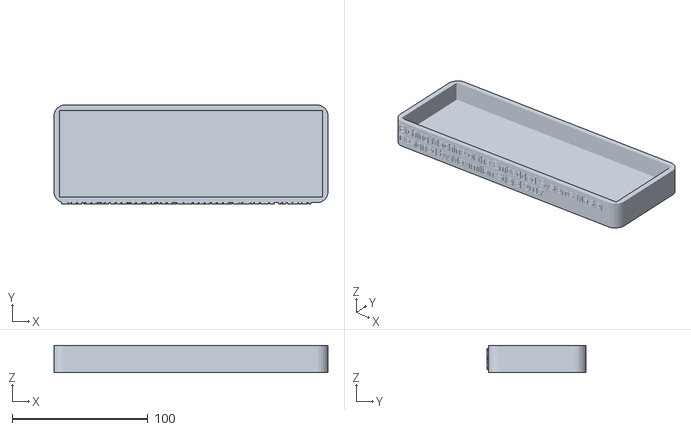
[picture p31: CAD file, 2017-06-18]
cad/output/pcb_holder_floor_prot.stl
202.0 x 72.9 x 20.0

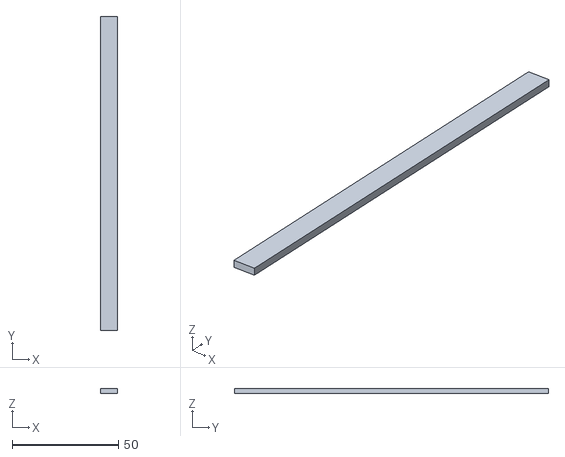
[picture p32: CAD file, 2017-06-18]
cad/output/pcb_holder_crossbar.stl
8.00 x 148.0 x 2.50

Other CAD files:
cad/uppsla_university.dxf
cad/output/pcb_holder_holder_r.stl
cad/dimensions.scad
cad/pcb_holder_crossbar.scad
cad/pcb_holder_floor_prot.scad
cad/pcb_holder_holder_l.scad
cad/pcb_holder_holder_r.scad
cad/pcb_holder_lid.scad
cad/roundy.scad

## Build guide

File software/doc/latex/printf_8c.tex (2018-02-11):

\hypertarget{printf_8c}{}\section{os/printf.c File Reference}
\label{printf_8c}\index{os/printf.\+c@{os/printf.\+c}}
{\ttfamily \#include $<$stdio.\+h$>$}\newline
{\ttfamily \#include $<$stdarg.\+h$>$}\newline
{\ttfamily \#include $<$string.\+h$>$}\newline
{\ttfamily \#include \char`\"{}stm32f10x.\+h\char`\"{}}\newline
{\ttfamily \#include \char`\"{}helpers.\+h\char`\"{}}\newline
{\ttfamily \#include \char`\"{}printf.\+h\char`\"{}}\newline
{\ttfamily \#include \char`\"{}../platform/usart.\+h\char`\"{}}\newline
{\ttfamily \#include \char`\"{}ossettings.\+h\char`\"{}}\newline
{\ttfamily \#include \char`\"{}error.\+h\char`\"{}}\newline
Include dependency graph for printf.\+c\+:\nopagebreak
\begin{figure}[H]
\begin{center}
\leavevmode
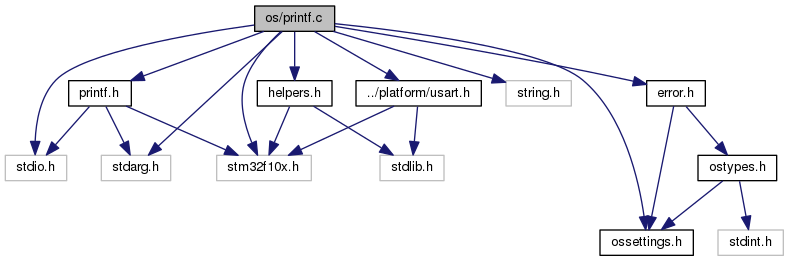
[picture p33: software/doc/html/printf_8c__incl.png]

\end{center}
\end{figure}
\subsection*{Functions}
\begin{DoxyCompactItemize}
\item 
int \hyperlink{printf_8c_ae2b707b3f94f0857c447e83c833b068a}{os\+Printf} (const char $\ast$iformat,...)
\end{DoxyCompactItemize}

\subsection{Function Documentation}
\mbox{\Hypertarget{printf_8c_ae2b707b3f94f0857c447e83c833b068a}\label{printf_8c_ae2b707b3f94f0857c447e83c833b068a}} 
\index{printf.\+c@{printf.\+c}!os\+Printf@{os\+Printf}}
\index{os\+Printf@{os\+Printf}!printf.\+c@{printf.\+c}}
\subsubsection{\texorpdfstring{os\+Printf()}{osPrintf()}}
{\footnotesize\ttfamily int os\+Printf (\begin{DoxyParamCaption}\item[{const char $\ast$}]{iformat,  }\item[{}]{... }\end{DoxyParamCaption})}

printf to be used by the OS user. Can be ported to another platform easily by just using another function to transmit one string with the U\+S\+A\+RT.

\begin{DoxyParams}{Parameters}
{\em iformat} & Currently supported are d integers c single characters s C strings f Floats with 4 decimals \%.xf Floats with x decimals \\
\hline
\end{DoxyParams}

\begin{DoxyRetVals}{Return values}
{\em Returns} & the number of characters printed (S\+U\+C\+C\+E\+SS) or -\/1 (F\+A\+I\+L\+U\+RE). \\
\hline
\end{DoxyRetVals}

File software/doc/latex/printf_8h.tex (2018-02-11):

\hypertarget{printf_8h}{}\section{os/printf.h File Reference}
\label{printf_8h}\index{os/printf.\+h@{os/printf.\+h}}

Lightweight version of G\+NU printf.  

{\ttfamily \#include $<$stdio.\+h$>$}\newline
{\ttfamily \#include $<$stdarg.\+h$>$}\newline
{\ttfamily \#include \char`\"{}stm32f10x.\+h\char`\"{}}\newline
Include dependency graph for printf.\+h\+:\nopagebreak
\begin{figure}[H]
\begin{center}
\leavevmode

\end{center}
\end{figure}
\subsection*{Functions}
\begin{DoxyCompactItemize}
\item 
int \hyperlink{printf_8h_ae2b707b3f94f0857c447e83c833b068a}{os\+Printf} (const char $\ast$iformat,...)
\end{DoxyCompactItemize}

\subsection{Detailed Description}
Lightweight version of G\+NU printf. 

\begin{DoxyAuthor}{Author}
Maximilian Stiefel 
\end{DoxyAuthor}
\begin{DoxyDate}{Date}
8 Jan 2018 
\end{DoxyDate}

\subsection{Function Documentation}
\mbox{\Hypertarget{printf_8h_ae2b707b3f94f0857c447e83c833b068a}\label{printf_8h_ae2b707b3f94f0857c447e83c833b068a}} 
\index{printf.\+h@{printf.\+h}!os\+Printf@{os\+Printf}}
\index{os\+Printf@{os\+Printf}!printf.\+h@{printf.\+h}}
\subsubsection{\texorpdfstring{os\+Printf()}{osPrintf()}}
{\footnotesize\ttfamily int os\+Printf (\begin{DoxyParamCaption}\item[{const char $\ast$}]{iformat,  }\item[{}]{... }\end{DoxyParamCaption})}

printf to be used by the OS user. Can be ported to another platform easily by just using another function to transmit one string with the U\+S\+A\+RT.

\begin{DoxyParams}{Parameters}
{\em iformat} & Currently supported are d integers c single characters s C strings f Floats with 4 decimals \%.xf Floats with x decimals \\
\hline
\end{DoxyParams}

\begin{DoxyRetVals}{Return values}
{\em Returns} & the number of characters printed (S\+U\+C\+C\+E\+SS) or -\/1 (F\+A\+I\+L\+U\+RE). \\
\hline
\end{DoxyRetVals}

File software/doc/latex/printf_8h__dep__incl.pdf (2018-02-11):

os/printf.h

os/error.c | os/heap.c | os/printf.c | os/scheduler.c

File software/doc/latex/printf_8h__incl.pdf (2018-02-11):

os/printf.h

stdio.h | stdarg.h | stm32f10x.h

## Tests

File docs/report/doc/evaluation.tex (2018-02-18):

%%%%%%%%%%%%%%%%%%%%%%%%%%%%%%%%%%%%%%%%%%%%%%%%%%%%%%%%%%%%%%%%%%%%%%%%%%%%%%%%%%%%%%
%% Author:      Nils Weber and Maximilian Stiefel
%% Date:        23.12.2017
%% University:  Uppsala Universitet
%% Department:  Institutionen för informationsteknologi 
%% Course:      Embedded Control System Project
%% Project:     PRECISELY CONTROLLED DIY ETCHING MACHINE 
%%				FOR USAGE AT HOME AND IN SMALL LABS
%%%%%%%%%%%%%%%%%%%%%%%%%%%%%%%%%%%%%%%%%%%%%%%%%%%%%%%%%%%%%%%%%%%%%%%%%%%%%%%%%%%%%%

\chapter{Evaluation}
\label{chap:evaluation}
% Describe the status of the work. What has been achieved?
The whole project is a strict work in progress, which is not finished yet. Different components have a different maturity. 
\newpar 
Tab. \ref{tab:os_status_quo} reflects the status quo of the \gls{OS}. It can certainly not keep up with modern \glspl{OS}. Nevertheless, it is easily comprehensible, because of its small footprint, and provides a bit another approach as a pure solution for real-time \glspl{OS} for embedded applications with useful accessories in this field.  

\begin{table}[H]
\centering
\begin{tabularx}{\textwidth}{lcX}
\textbf{Component} & \textbf{Working} & \textbf{Problem} \\\hline
Non-preemptive Scheduling & \checkmark	& Round-robin scheduling is not guaranteed among tasks having the same priority. \\
Preemptive Scheduling & \checkmark	& \\	
System Tick Configuration & \checkmark	& \\
Error Logging & \checkmark	& Only supports one sink (\gls{USART}) so far. \\
printf & \checkmark	& Only supports the options \%d, \%f, \%c and \%s currently. \\
Queues & \checkmark	& Only supports one kind of queue, which is useful for a producer-consumer scenarios. \\
Semaphores & & \\
\gls{PID} controller infrastructure & & \\
Console & & \\
\hline
\end{tabularx}
\caption{Status Quo \gls{OS}}
\label{tab:os_status_quo}
\end{table}

The \gls{UV} light hardware has been simulated with the help of \myemph{LTSpice} quite extensively. After gaining support from Yi Wang and convincing the department to pay these companies for their products and services respectively, both \glspl{PCB} introduced earlier have been manufactured in China by the company \myemph{Elecrow} (\hyperref{http://www.elecrow.com}{Elecrow}). Also, the components have been ordered in the USA from the distributor \myemph{Digikey} and are available. The boards have not yet been assembled and tested. The planned intend to get rid of mercury, mentioned in chapter \ref{chap:background}, has been pursued consequently. It is an absolutely revolutionary feature, that this \gls{UV} exposure unit does not use fluorescent lamps like the most common type the competitors offer on the market right now. A housing has been built from wood, which is cheaper and rather environmentally friendly. The current mechanics allow single-sided \gls{UV} light exposure.  

\begin{table}[H]
\centering
\begin{tabularx}{\textwidth}{lcX}
\textbf{Component} & \textbf{Working} & \textbf{Problem} \\\hline
No mercury & \checkmark & \\
Double-sided UV light exposure & & \\
Precisely controlled light intensity & \checkmark & \\
Digital and elegant user interface & \checkmark & \\
Hardware design ready & \checkmark & \\
Hardware assembled and tested & & \\
No expensive metal housings & \checkmark & \\
\gls{DAC} driver & & \\
\gls{OLED} driver & & \\
Rotary encoder driver & & \\
\hline
\end{tabularx}
\caption{Status Quo \gls{UV} light}
\label{tab:os_status_quo}
\end{table}

The etching bath temperature control is in an earlier stage of development, where success was for a long time hindered by a driver issue with the \gls{ADC} on a similar STM32-chip. For development the STM32L073RZ was used, for the simple reason of immediate availability. However, the \gls{ADC} on this specific chip has had problems reading the values properly until now. Without actual data from the temperature sensor the rest of the system could only be implemented but not tested. A simple on-off controller has been tested successfully, the implementation with proportional and inertia correction has not yet been tested successfully.

\begin{table}[H]
\centering
\begin{tabularx}{\textwidth}{lcX}
\textbf{Component} & \textbf{Working} & \textbf{Problem} \\\hline
Digital and elegant user interface & \checkmark & \\
Hardware design ready & & \\
Hardware assembled and tested & & Heater needs to be "hacked" for control \\
Additive manufactured housing & \checkmark & PCB holder needs improvement \\
\gls{ADC} driver for NTC & \checkmark & \\
\gls{I2C} driver & \checkmark & \\
\gls{OLED} driver & \checkmark & \\
Rotary encoder driver & \checkmark & Low-pass filter missing \\
On-off controller & \checkmark & \\
On-off controller with corrections & & \\
\hline
\end{tabularx}
\caption{Status Quo etching bath}
\label{tab:etching_status_quo}
\end{table}

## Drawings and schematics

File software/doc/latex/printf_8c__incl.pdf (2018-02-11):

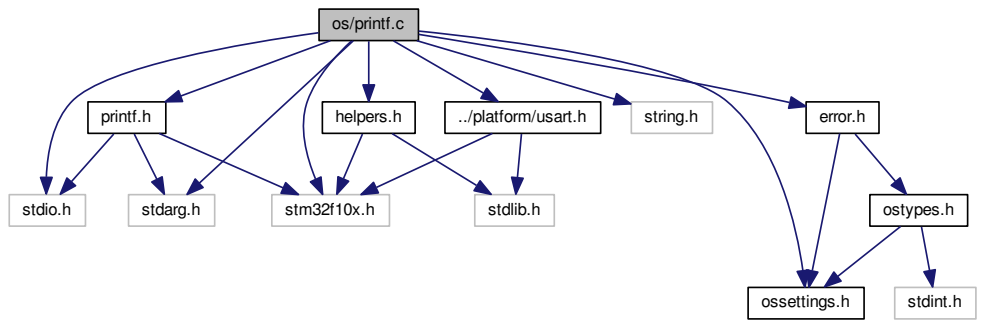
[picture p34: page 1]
os/printf.c; stdio.h; stdarg.h; string.h; stm32f10x.h; printf.h; helpers.h; ../platform/usart.h; ossettings.h; error.h; stdlib.h; ostypes.h; stdint.h

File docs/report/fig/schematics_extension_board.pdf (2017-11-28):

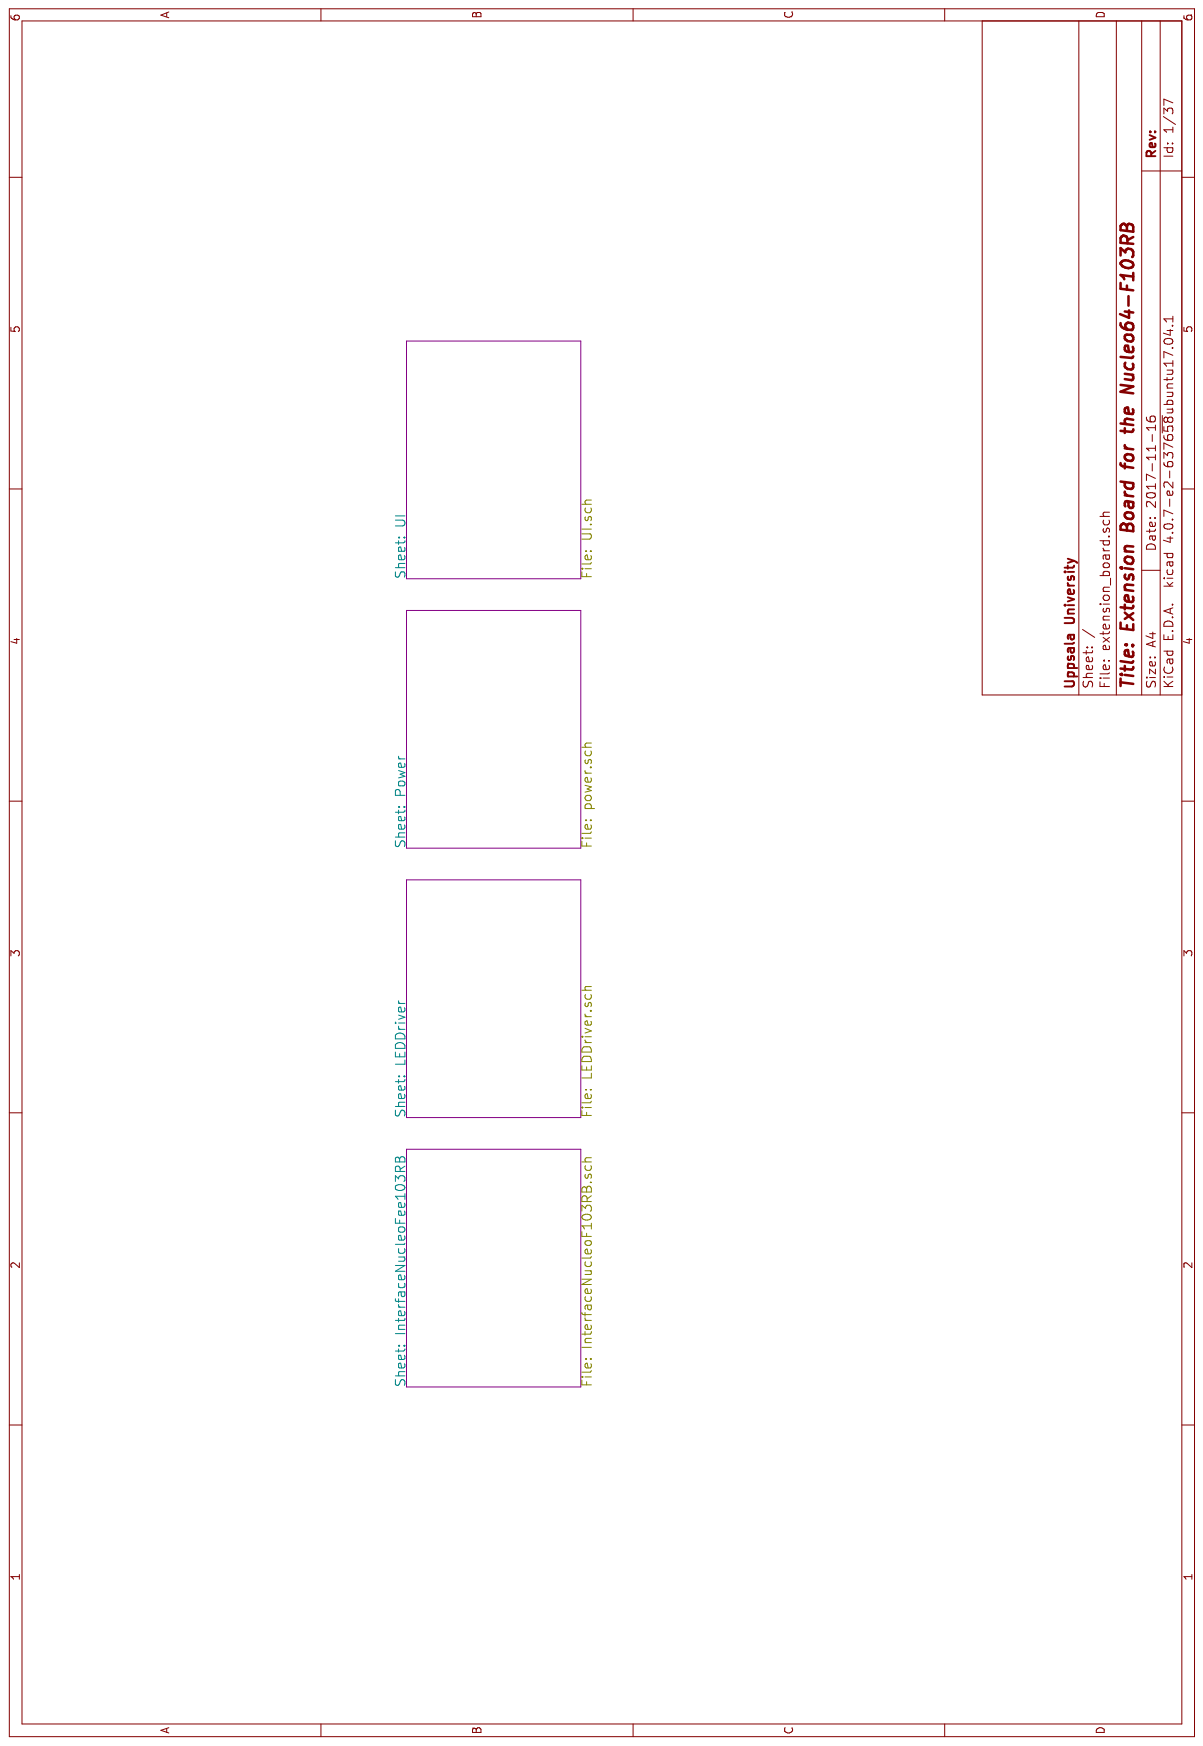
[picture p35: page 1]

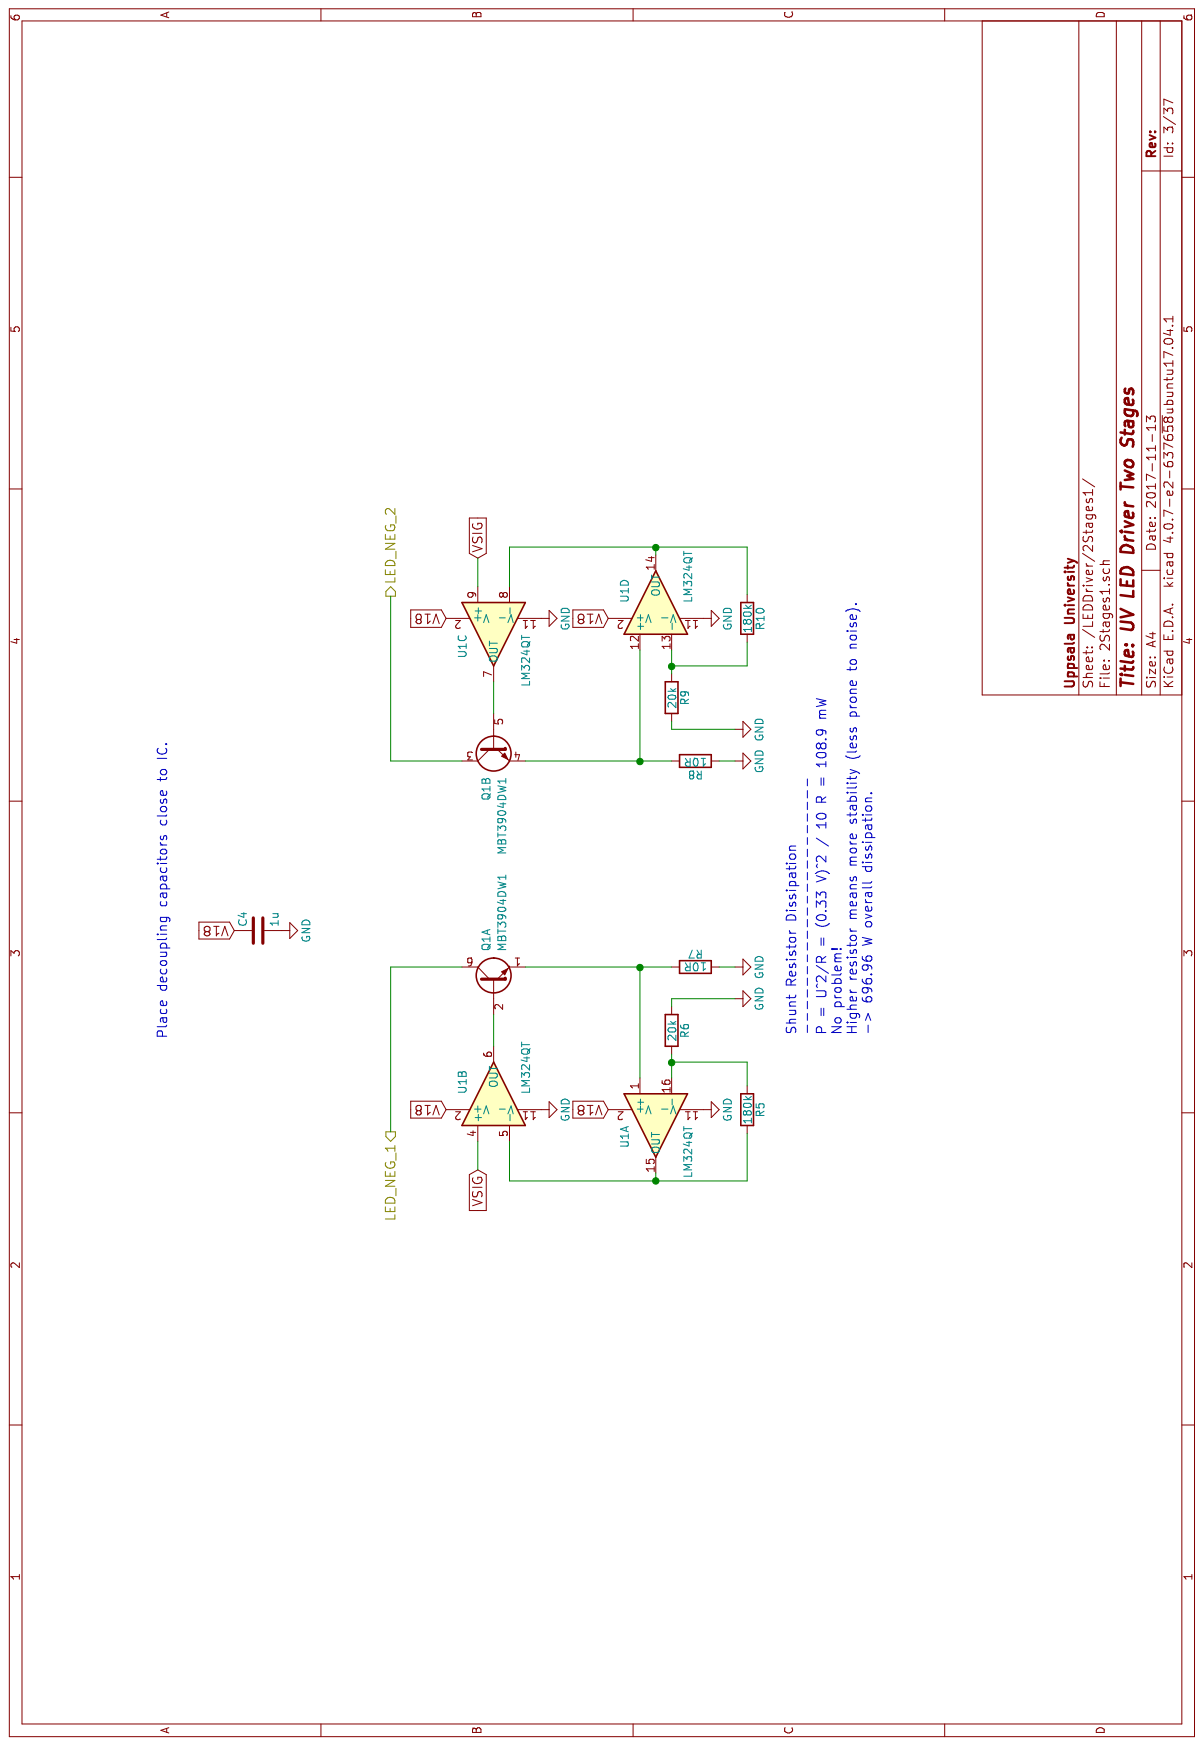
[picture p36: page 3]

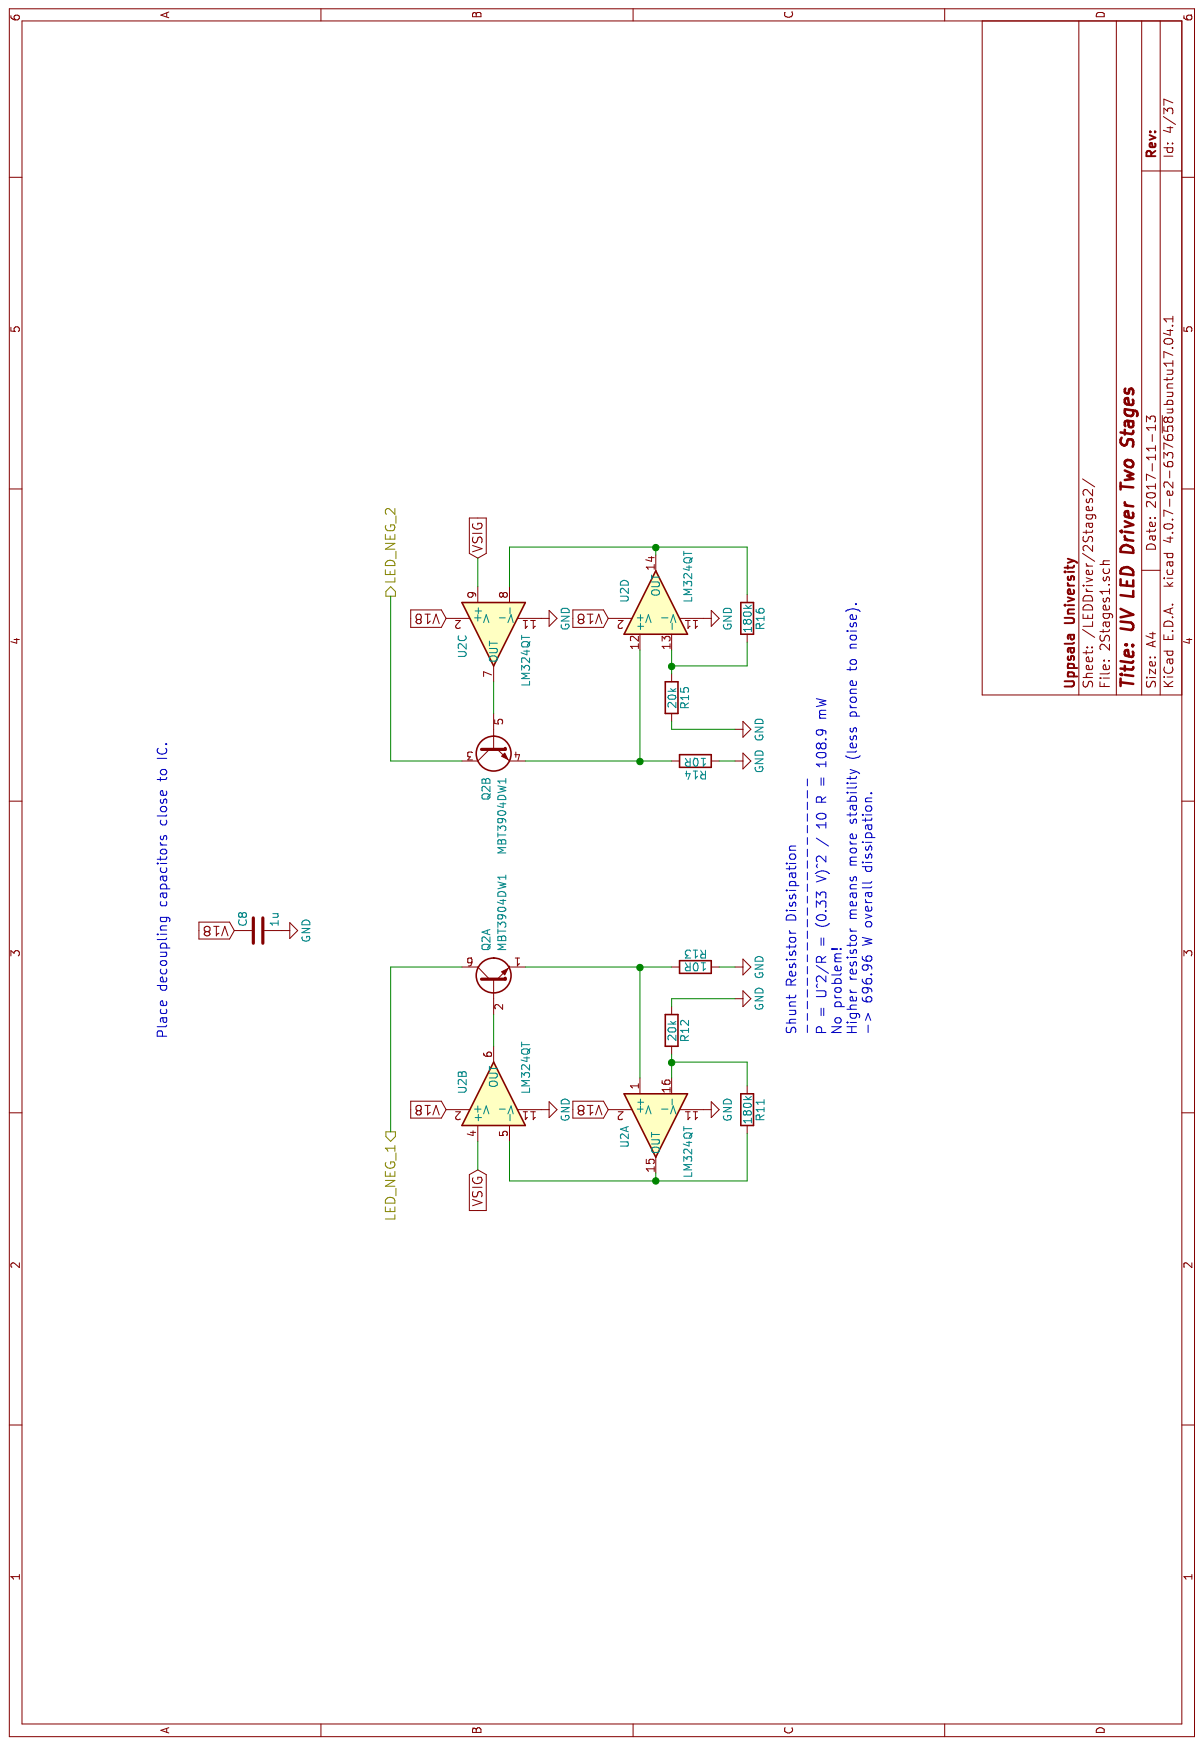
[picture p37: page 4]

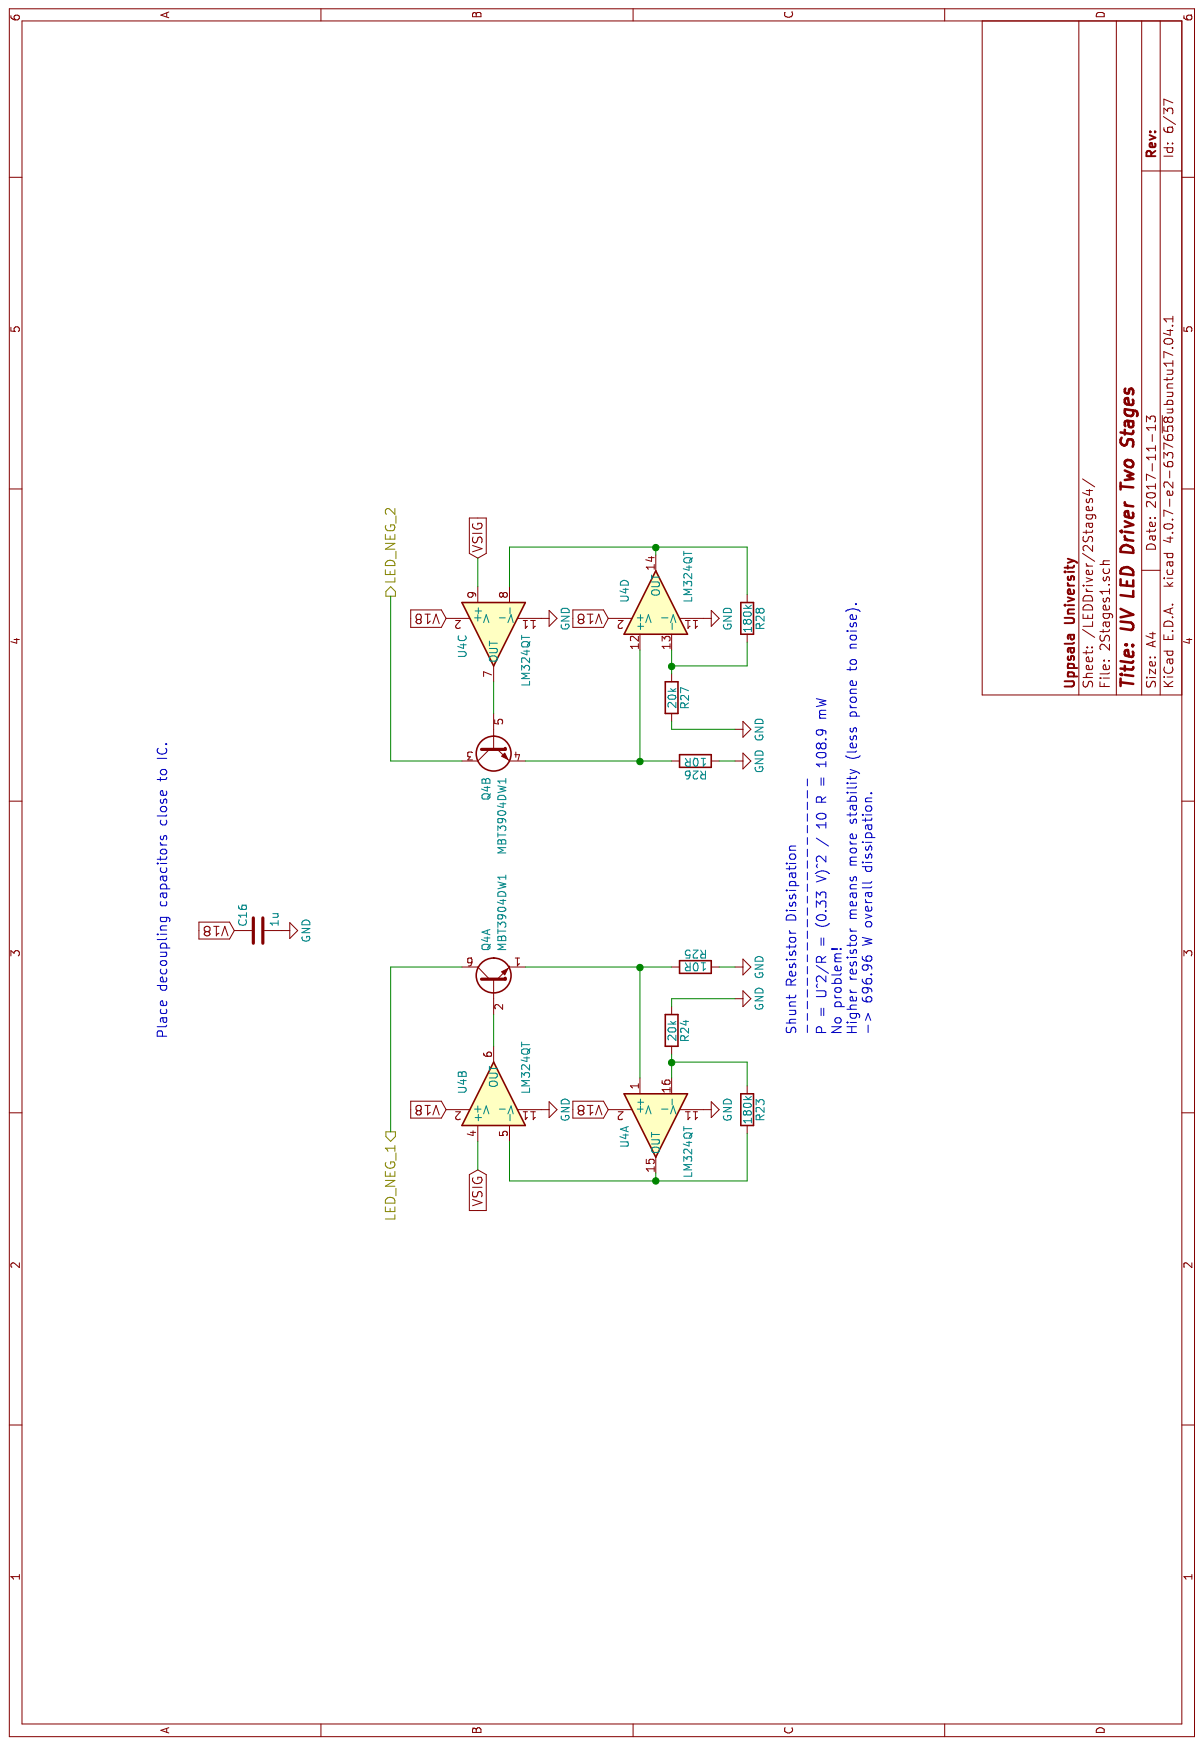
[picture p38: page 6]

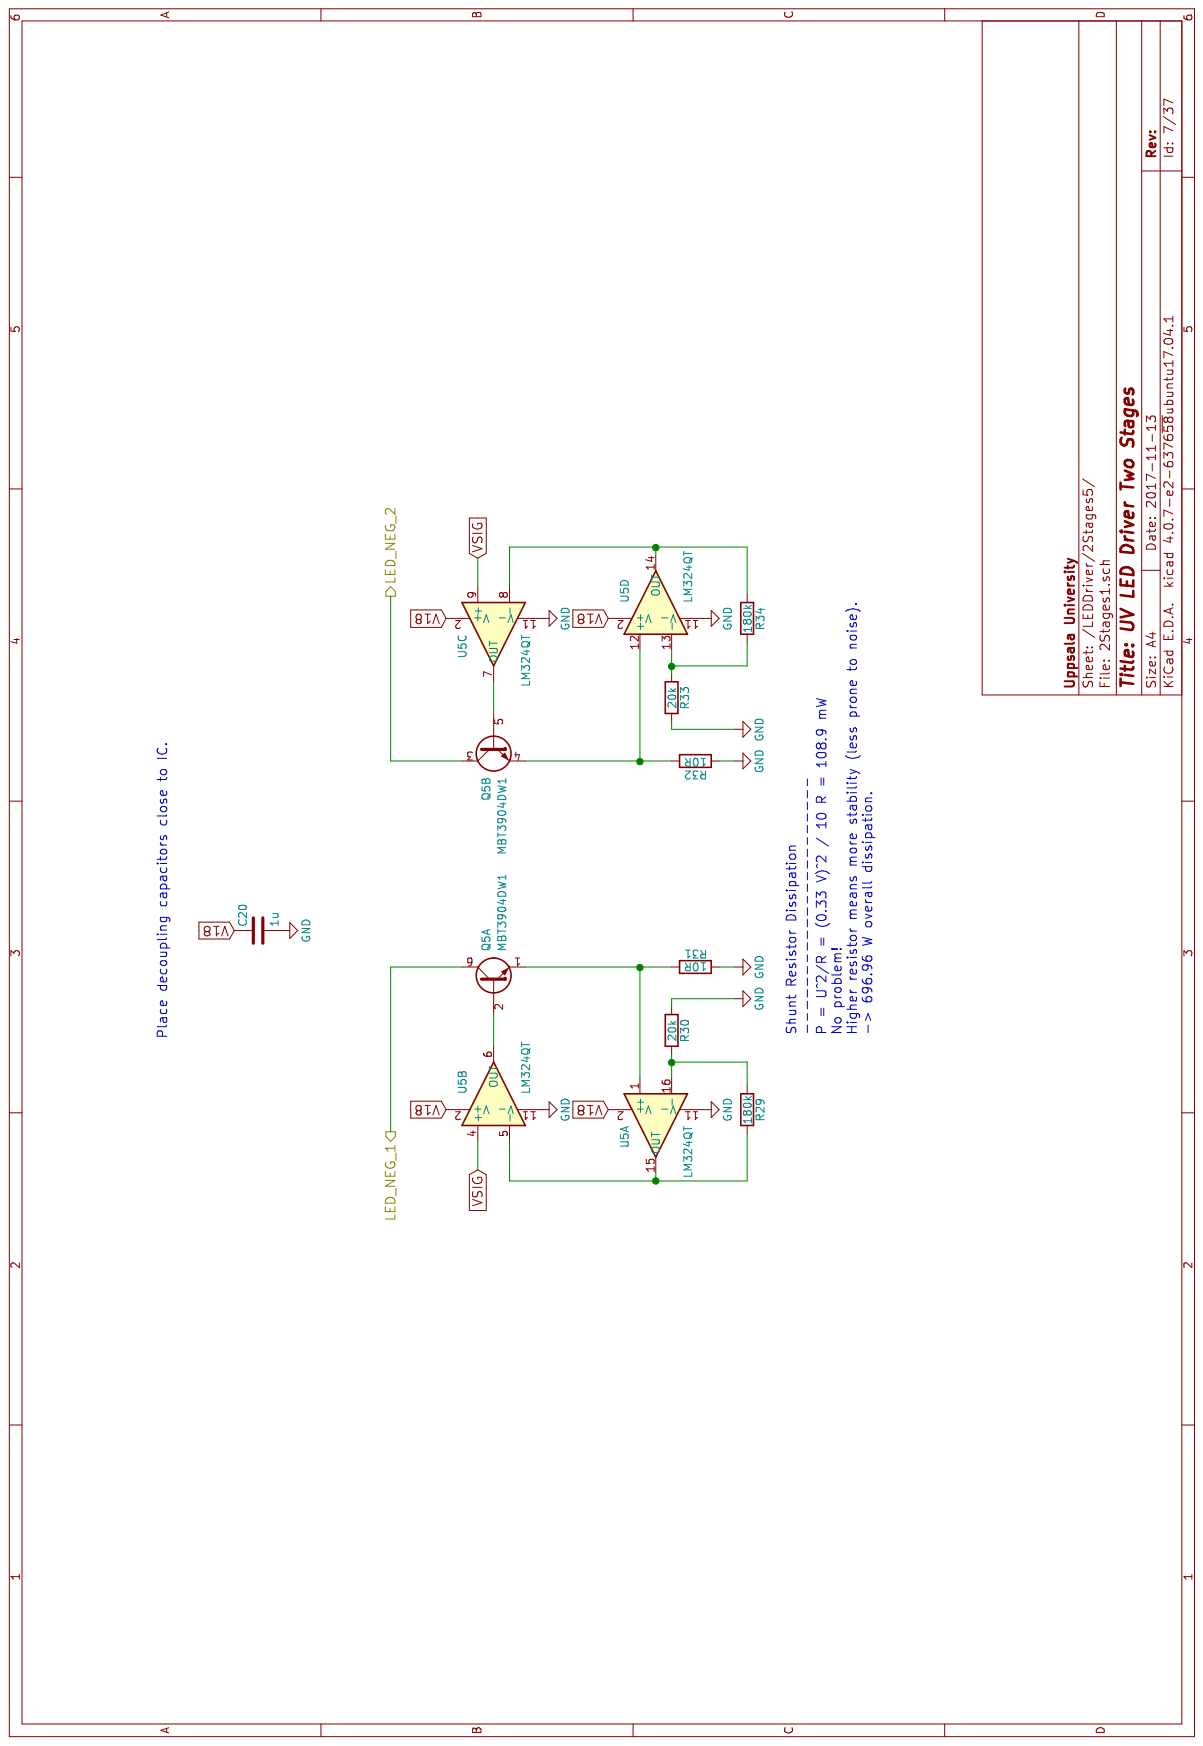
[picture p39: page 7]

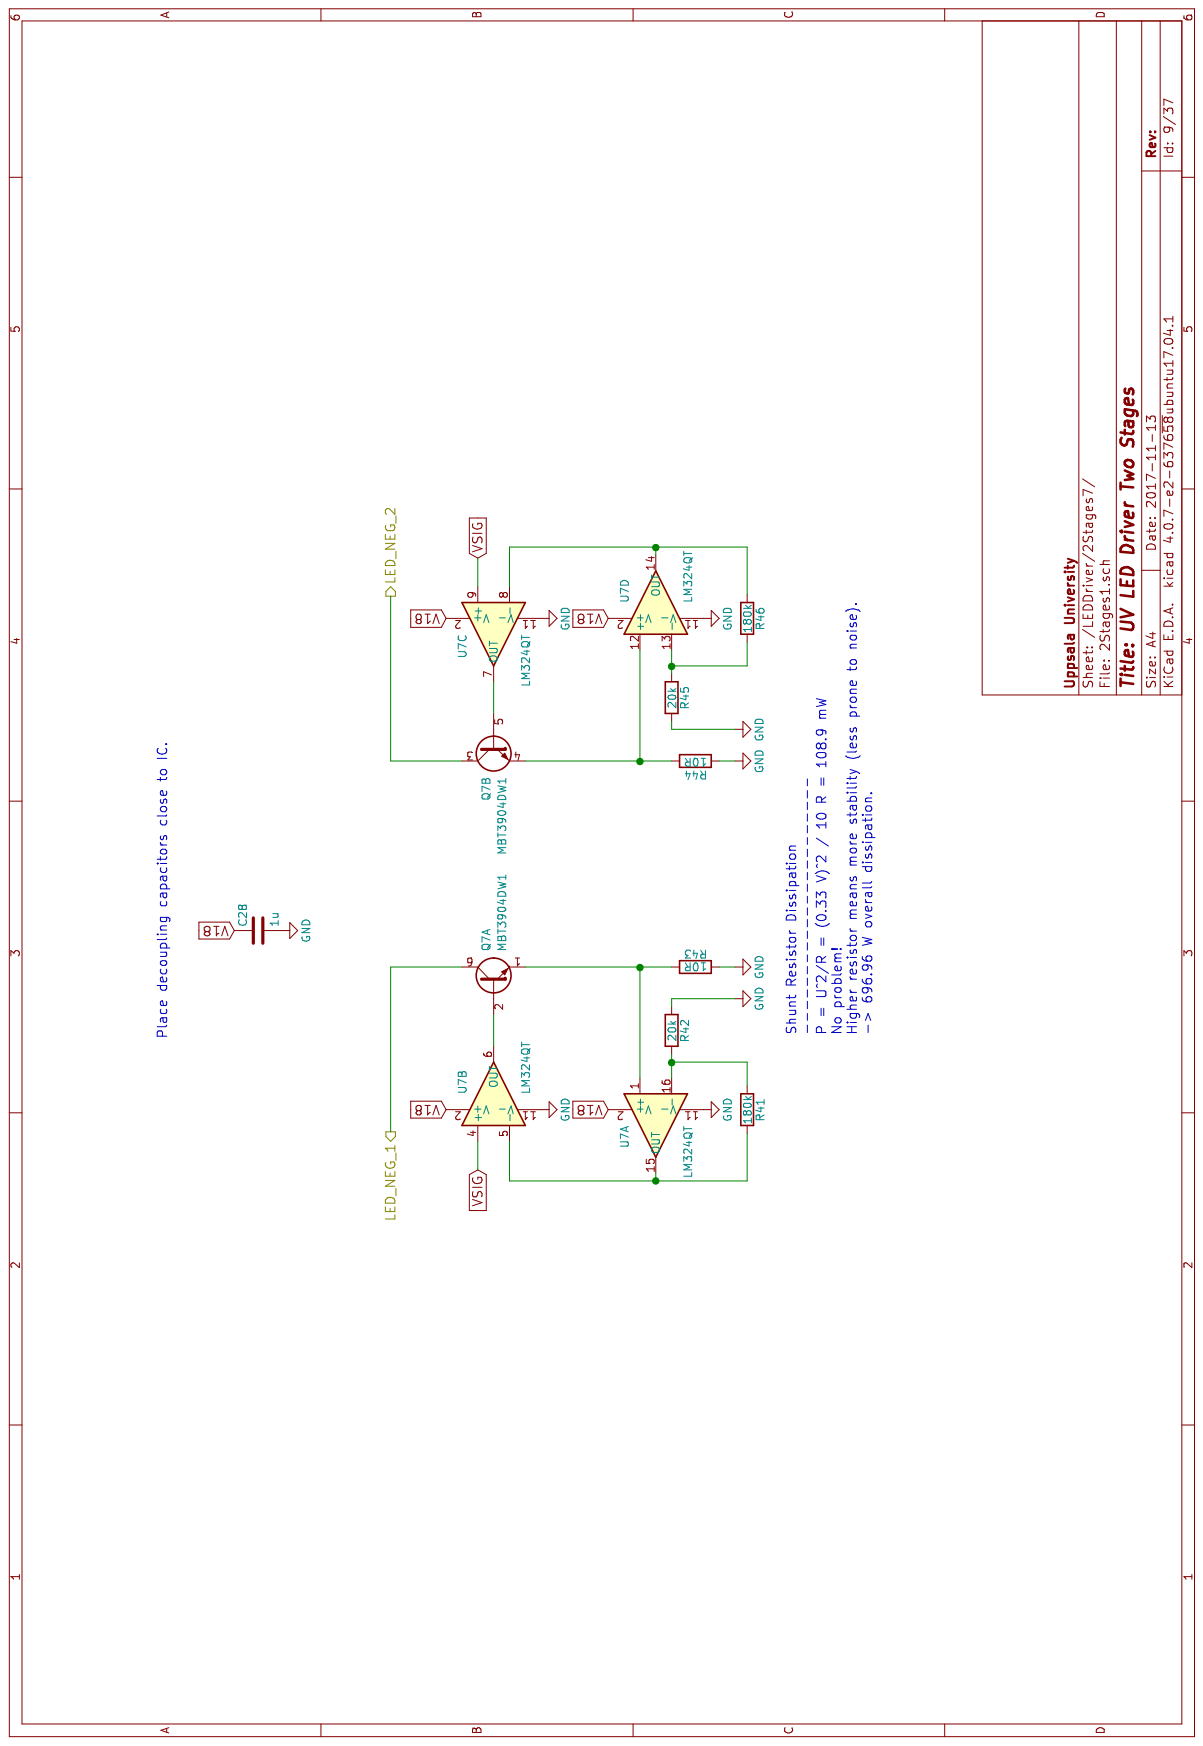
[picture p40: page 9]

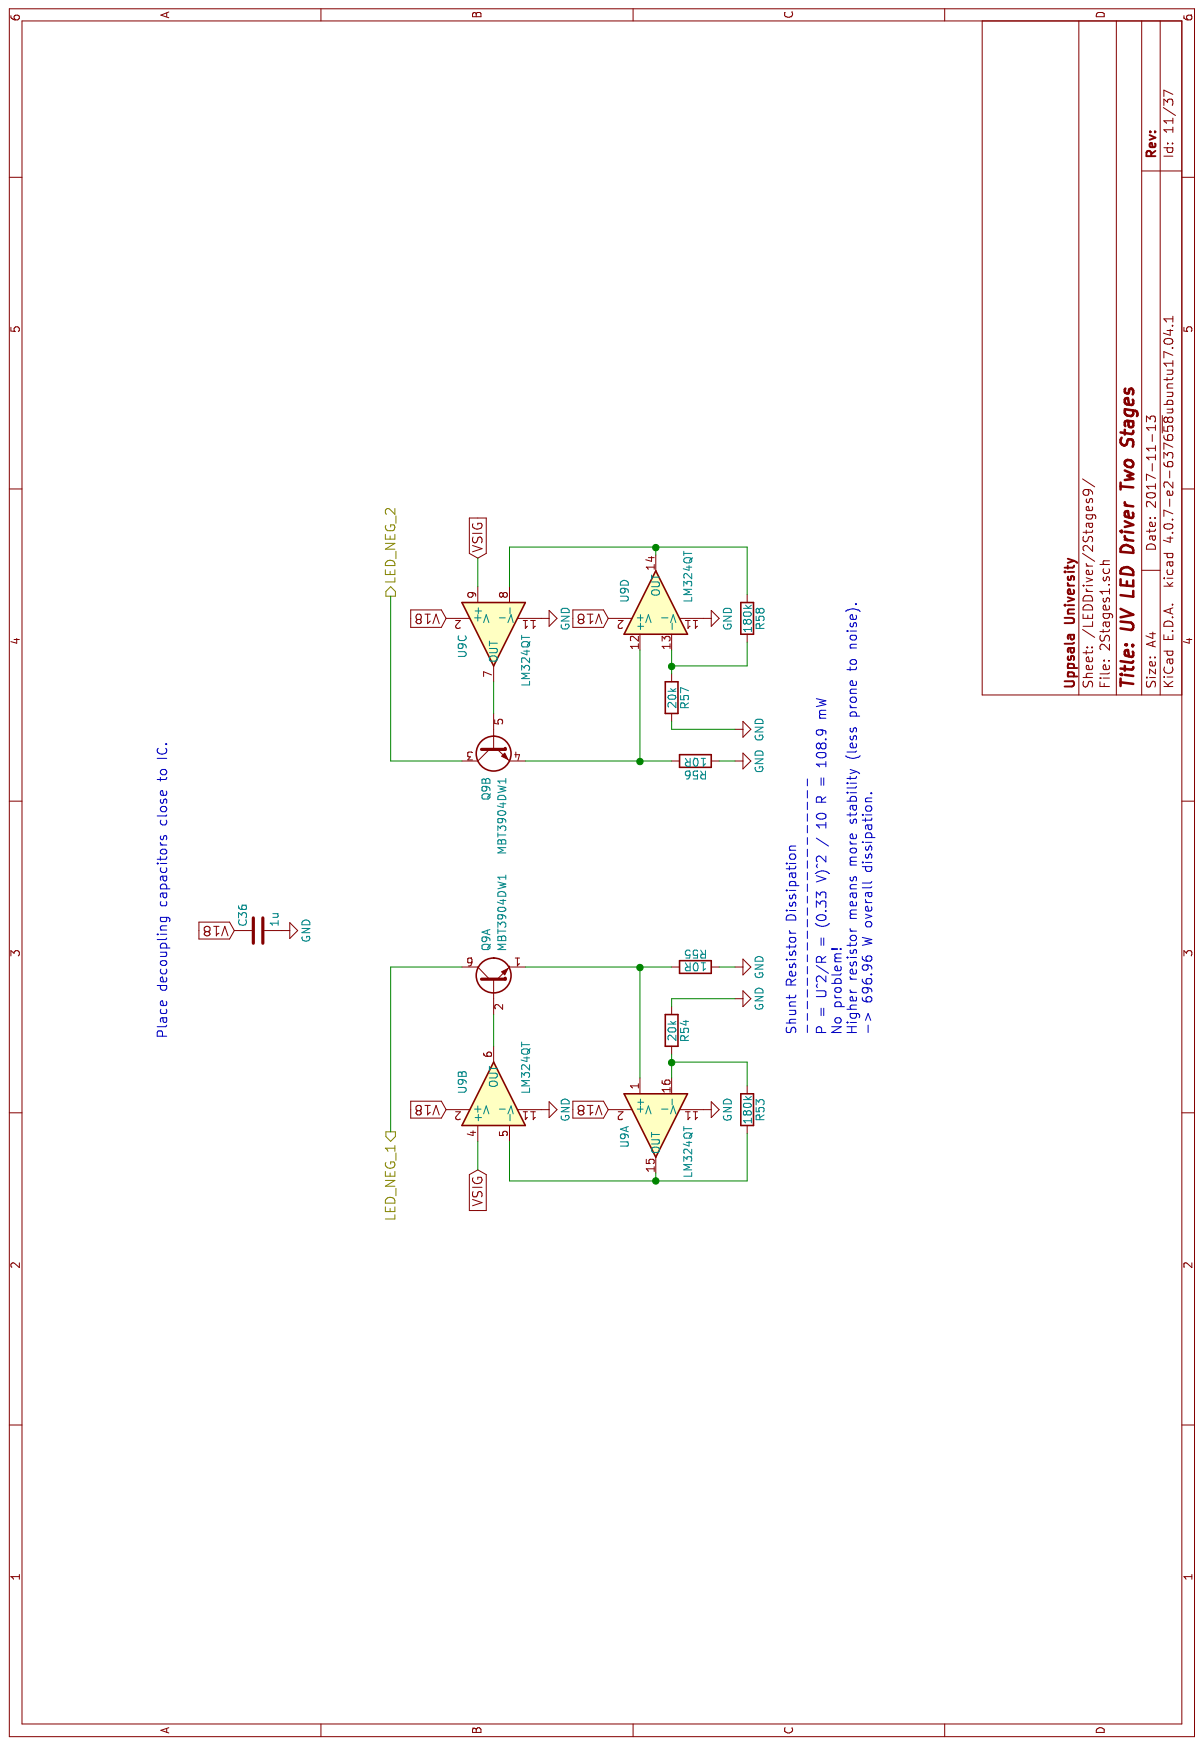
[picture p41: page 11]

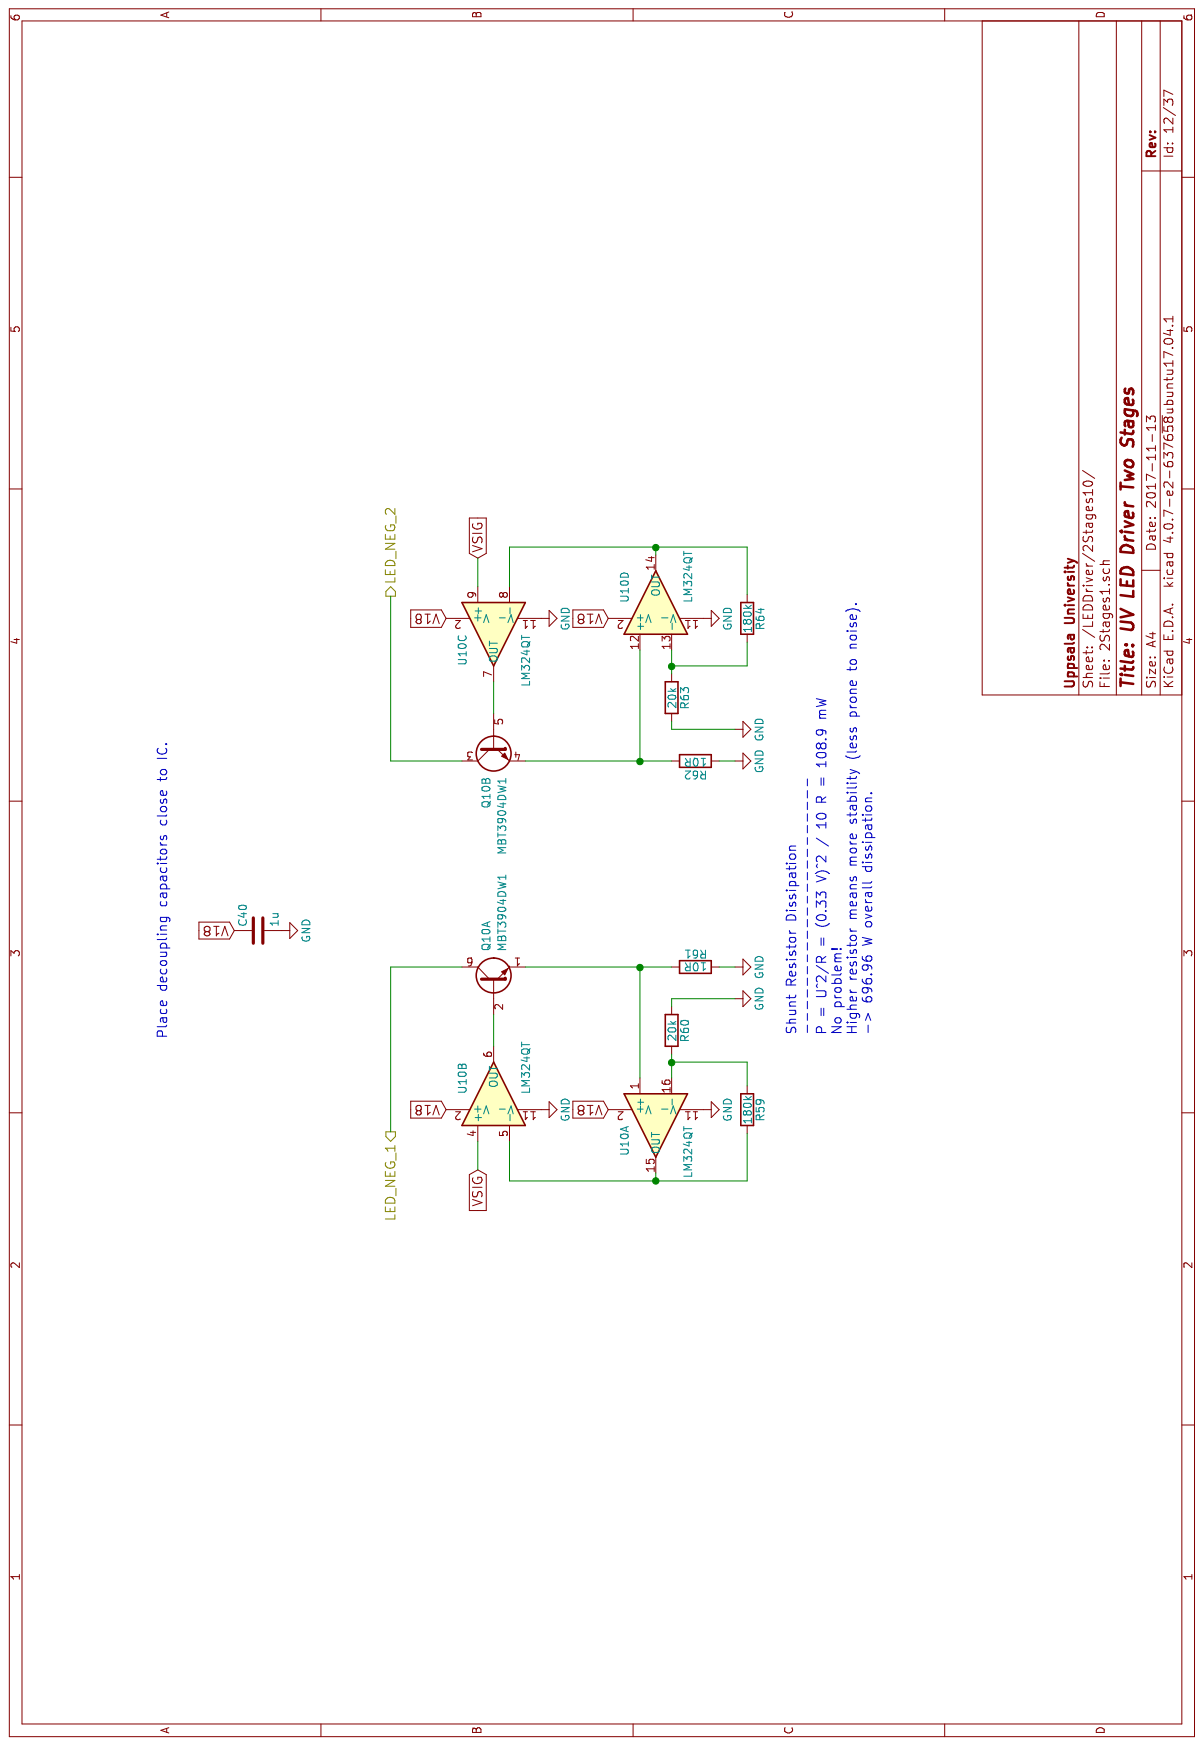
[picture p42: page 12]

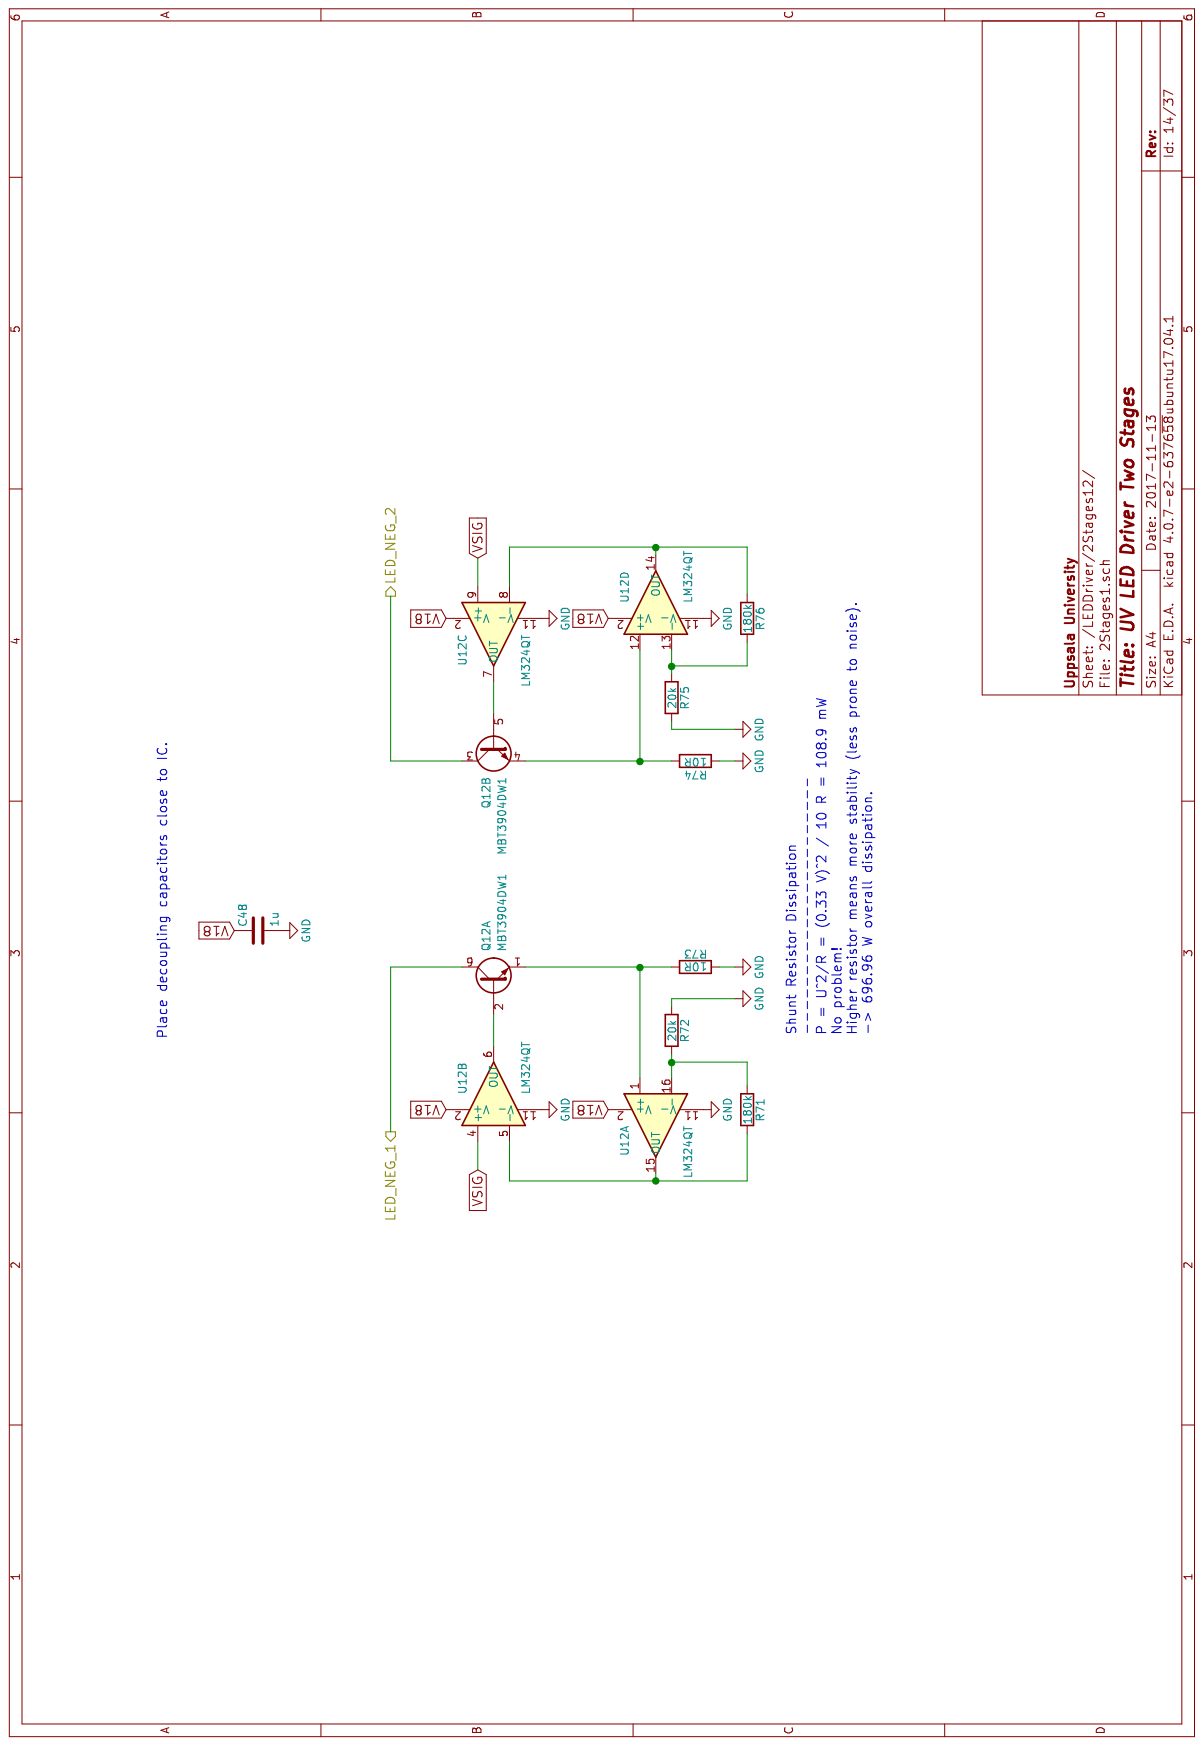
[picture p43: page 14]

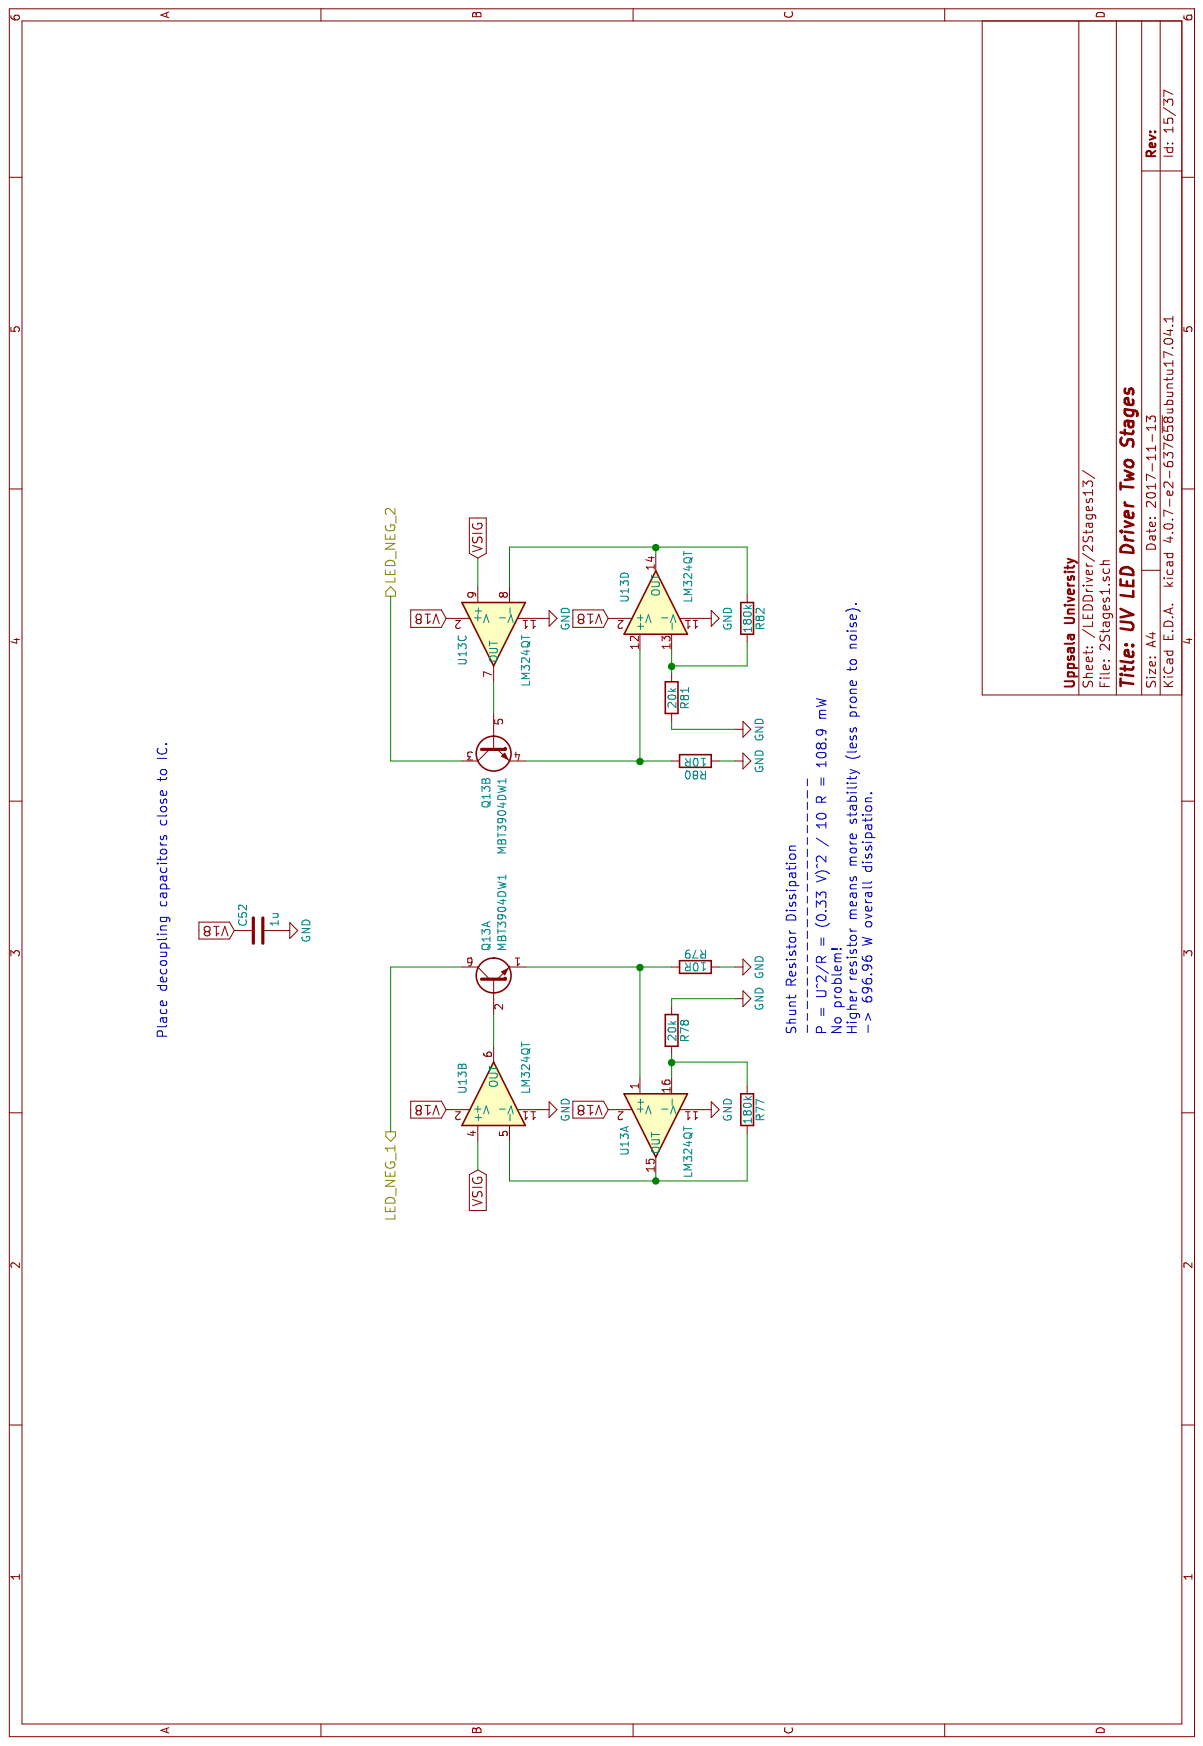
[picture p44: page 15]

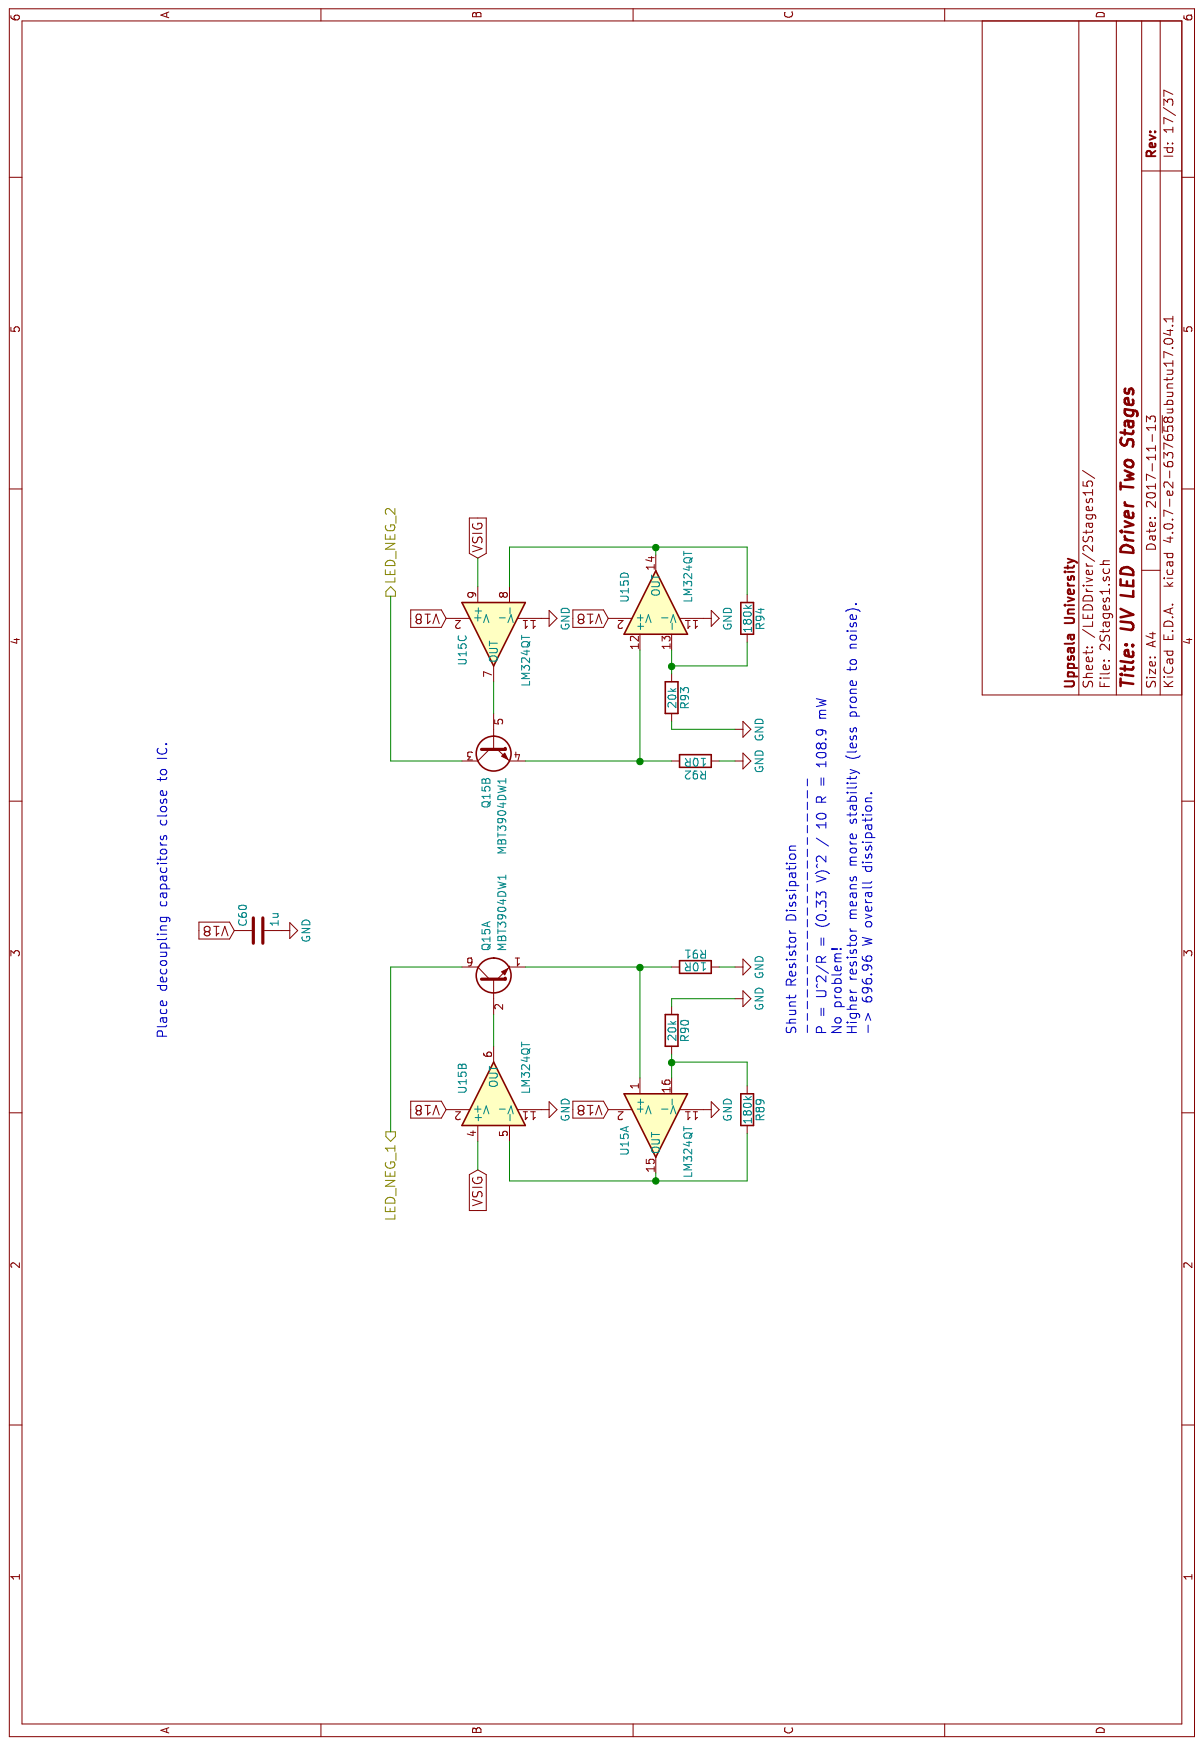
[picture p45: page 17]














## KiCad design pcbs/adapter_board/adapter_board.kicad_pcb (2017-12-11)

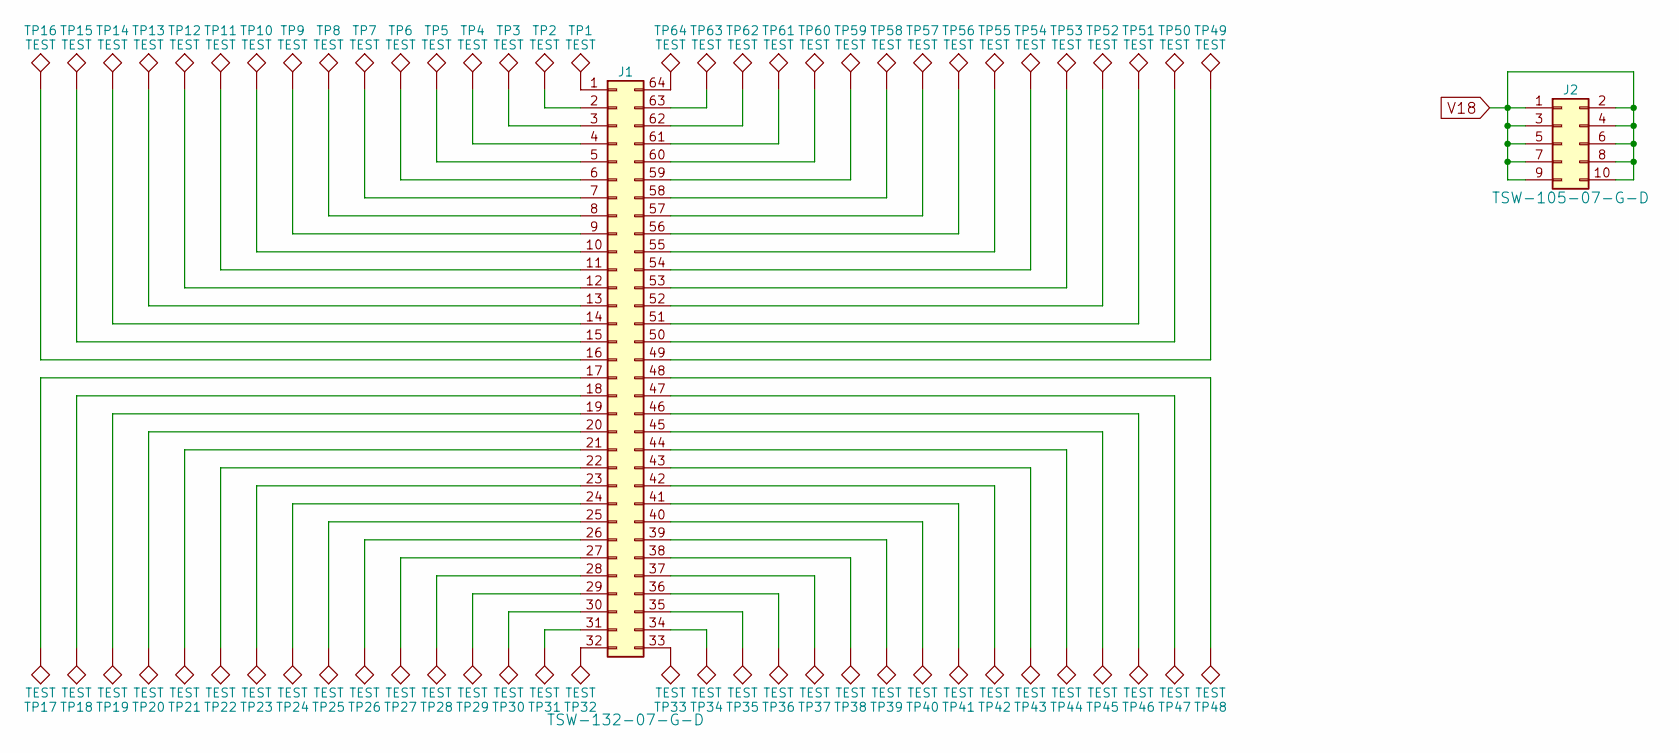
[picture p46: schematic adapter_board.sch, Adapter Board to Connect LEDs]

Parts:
J1: Conn_02x32_Counter_Clockwise; Pin_Header_Straight_2x32_Pitch2.54mm
J2: Conn_02x05_Odd_Even; Pin_Header_Straight_2x05_Pitch2.54mm
TP1, TP2, TP3, TP4, TP5, TP6, TP7, TP8, TP9, TP10, TP11, TP12, TP13, TP14, TP15, TP16, TP17, TP18, TP19, TP20, TP21, TP22, TP23, TP24, TP25, TP26, TP27, TP28, TP29, TP30, TP31, TP32, TP33, TP34, TP35, TP36, TP37, TP38, TP39, TP40, TP41, TP42, TP43, TP44, TP45, TP46, TP47, TP48, TP49, TP50, TP51, TP52, TP53, TP54, TP55, TP56, TP57, TP58, TP59, TP60, TP61, TP62, TP63, TP64: TEST; TP_SMD_2mmx5mm

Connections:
unnamed: J1.1, TP1.1
unnamed: J1.2, TP2.1
unnamed: J1.3, TP3.1
unnamed: J1.4, TP4.1
unnamed: J1.5, TP5.1
unnamed: J1.6, TP6.1
unnamed: J1.7, TP7.1
unnamed: J1.8, TP8.1
unnamed: J1.9, TP9.1
unnamed: J1.10, TP10.1
unnamed: J1.11, TP11.1
unnamed: J1.12, TP12.1
unnamed: J1.13, TP13.1
unnamed: J1.14, TP14.1
unnamed: J1.15, TP15.1
unnamed: J1.16, TP16.1
unnamed: J1.17, TP17.1
unnamed: J1.18, TP18.1
unnamed: J1.19, TP19.1
unnamed: J1.20, TP20.1
unnamed: J1.21, TP21.1
unnamed: J1.22, TP22.1
unnamed: J1.23, TP23.1
unnamed: J1.24, TP24.1
unnamed: J1.25, TP25.1
unnamed: J1.26, TP26.1
unnamed: J1.27, TP27.1
unnamed: J1.28, TP28.1
unnamed: J1.29, TP29.1
unnamed: J1.30, TP30.1
unnamed: J1.31, TP31.1
unnamed: J1.32, TP32.1
unnamed: J1.33, TP33.1
unnamed: J1.34, TP34.1
unnamed: J1.35, TP35.1
unnamed: J1.36, TP36.1
unnamed: J1.37, TP37.1
unnamed: J1.38, TP38.1
unnamed: J1.39, TP39.1
unnamed: J1.40, TP40.1
unnamed: J1.41, TP41.1
unnamed: J1.42, TP42.1
unnamed: J1.43, TP43.1
unnamed: J1.44, TP44.1
unnamed: J1.45, TP45.1
unnamed: J1.46, TP46.1
unnamed: J1.47, TP47.1
unnamed: J1.48, TP48.1
unnamed: J1.49, TP49.1
unnamed: J1.50, TP50.1
unnamed: J1.51, TP51.1
unnamed: J1.52, TP52.1
unnamed: J1.53, TP53.1
unnamed: J1.54, TP54.1
unnamed: J1.55, TP55.1
unnamed: J1.56, TP56.1
unnamed: J1.57, TP57.1
unnamed: J1.58, TP58.1
unnamed: J1.59, TP59.1
unnamed: J1.60, TP60.1
unnamed: J1.61, TP61.1
unnamed: J1.62, TP62.1
unnamed: J1.63, TP63.1
unnamed: J1.64, TP64.1
V18: J2.1, J2.2, J2.3, J2.4, J2.5, J2.6, J2.7, J2.8, J2.9, J2.10

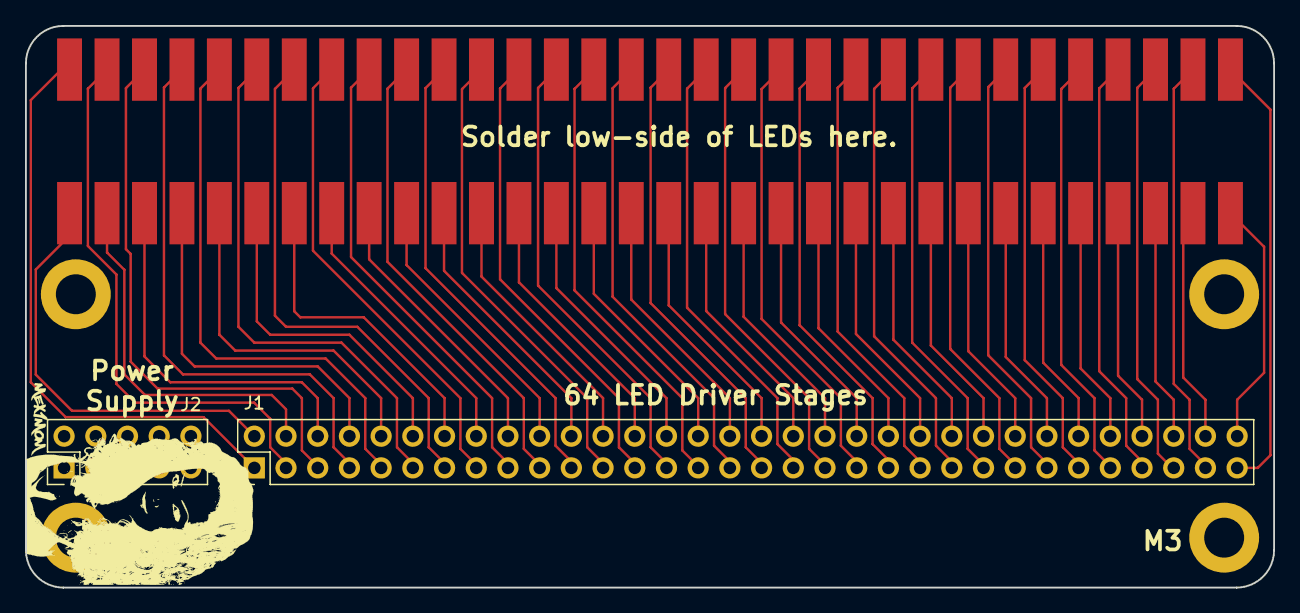
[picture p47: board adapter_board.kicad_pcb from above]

Board: 2 copper layers, 100.0 x 45.0 mm, 66 parts (0 on the bottom side), 65 nets.

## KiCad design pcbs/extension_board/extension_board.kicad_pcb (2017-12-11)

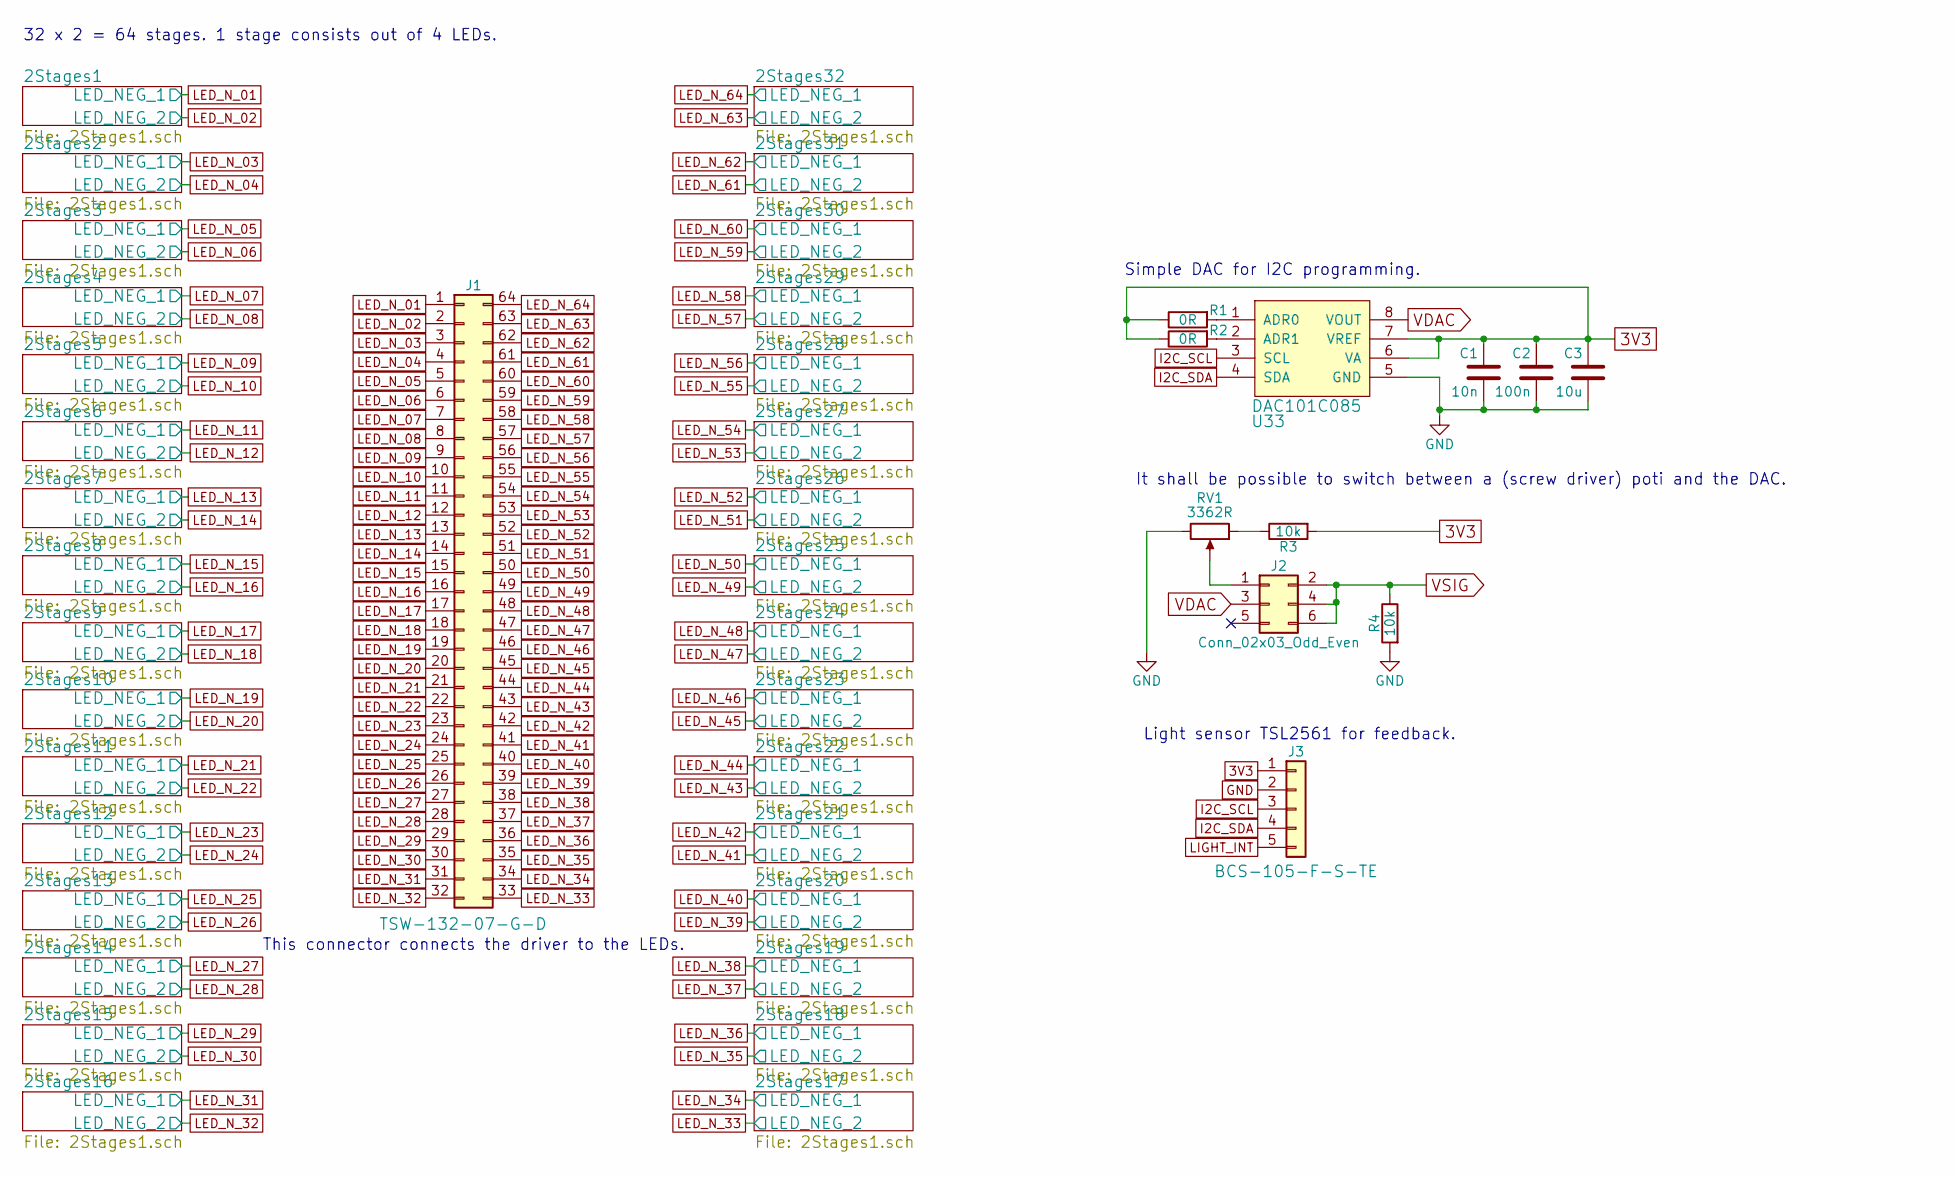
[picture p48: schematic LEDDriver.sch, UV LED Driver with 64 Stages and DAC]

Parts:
C1: 10n; R_0603; Digikey 311-1085-1-ND
C2: 100n; R_0603; Digikey 311-1088-1-ND
C3: 10u; R_0603; Digikey 490-6403-6-ND
J1: Conn_02x32_Counter_Clockwise; Pin_Header_Straight_2x32_Pitch2.54mm
J2: Conn_02x03_Odd_Even; Pin_Header_Straight_2x03_Pitch2.54mm
J3: Conn_01x05; Pin_Header_Straight_1x05_Pitch2.54mm
R1, R2: 0R; R_0603; Digikey 311-0.0GRCT-ND
R3, R4: 10k; R_0603; Digikey 311-10KGRCT-ND
RV1: 3362R; Burns_3362R; Digikey 3362R-103LF-ND
U33: DAC101C085; VSSOP-8_3.0x3.0mm_Pitch0.65mm; Digikey DAC101C085CIMM/NOPBCT-ND

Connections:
+3V3: C1.1, C2.1, C3.1, J3.1, R1.1, R2.1, R3.2, U33.6 (VA), U33.7 (VREF); also elsewhere on the board
GND: C1.2, C2.2, C3.2, J3.2, R4.2, RV1.3, U33.5 (GND); also elsewhere on the board
I2C_SCL: J3.3, U33.3 (SCL); also elsewhere on the board
I2C_SDA: J3.4, U33.4 (SDA); also elsewhere on the board
LED_N_01: J1.1; also elsewhere on the board
LED_N_02: J1.2; also elsewhere on the board
LED_N_03: J1.3; also elsewhere on the board
LED_N_04: J1.4; also elsewhere on the board
LED_N_05: J1.5; also elsewhere on the board
LED_N_06: J1.6; also elsewhere on the board
LED_N_07: J1.7; also elsewhere on the board
LED_N_08: J1.8; also elsewhere on the board
LED_N_09: J1.9; also elsewhere on the board
LED_N_10: J1.10; also elsewhere on the board
LED_N_11: J1.11; also elsewhere on the board
LED_N_12: J1.12; also elsewhere on the board
LED_N_13: J1.13; also elsewhere on the board
LED_N_14: J1.14; also elsewhere on the board
LED_N_15: J1.15; also elsewhere on the board
LED_N_16: J1.16; also elsewhere on the board
LED_N_17: J1.17; also elsewhere on the board
LED_N_18: J1.18; also elsewhere on the board
LED_N_19: J1.19; also elsewhere on the board
LED_N_20: J1.20; also elsewhere on the board
LED_N_21: J1.21; also elsewhere on the board
LED_N_22: J1.22; also elsewhere on the board
LED_N_23: J1.23; also elsewhere on the board
LED_N_24: J1.24; also elsewhere on the board
LED_N_25: J1.25; also elsewhere on the board
LED_N_26: J1.26; also elsewhere on the board
LED_N_27: J1.27; also elsewhere on the board
LED_N_28: J1.28; also elsewhere on the board
LED_N_29: J1.29; also elsewhere on the board
LED_N_30: J1.30; also elsewhere on the board
LED_N_31: J1.31; also elsewhere on the board
LED_N_32: J1.32; also elsewhere on the board
LED_N_33: J1.33; also elsewhere on the board
LED_N_34: J1.34; also elsewhere on the board
LED_N_35: J1.35; also elsewhere on the board
LED_N_36: J1.36; also elsewhere on the board
LED_N_37: J1.37; also elsewhere on the board
LED_N_38: J1.38; also elsewhere on the board
LED_N_39: J1.39; also elsewhere on the board
LED_N_40: J1.40; also elsewhere on the board
LED_N_41: J1.41; also elsewhere on the board
LED_N_42: J1.42; also elsewhere on the board
LED_N_43: J1.43; also elsewhere on the board
LED_N_44: J1.44; also elsewhere on the board
LED_N_45: J1.45; also elsewhere on the board
LED_N_46: J1.46; also elsewhere on the board
LED_N_47: J1.47; also elsewhere on the board
LED_N_48: J1.48; also elsewhere on the board
LED_N_49: J1.49; also elsewhere on the board
LED_N_50: J1.50; also elsewhere on the board
LED_N_51: J1.51; also elsewhere on the board
LED_N_52: J1.52; also elsewhere on the board
LED_N_53: J1.53; also elsewhere on the board
LED_N_54: J1.54; also elsewhere on the board
LED_N_55: J1.55; also elsewhere on the board
LED_N_56: J1.56; also elsewhere on the board
LED_N_57: J1.57; also elsewhere on the board
LED_N_58: J1.58; also elsewhere on the board
LED_N_59: J1.59; also elsewhere on the board
LED_N_60: J1.60; also elsewhere on the board
LED_N_61: J1.61; also elsewhere on the board
LED_N_62: J1.62; also elsewhere on the board
LED_N_63: J1.63; also elsewhere on the board
LED_N_64: J1.64; also elsewhere on the board
LIGHT_INT: J3.5; also elsewhere on the board
unnamed: J2.1, RV1.2
unnamed: R1.2, U33.1 (ADR0)
unnamed: R2.2, U33.2 (ADR1)
unnamed: R3.1, RV1.1
VDAC: J2.3, U33.8 (VOUT)
VSIG: J2.2, J2.4, J2.6, R4.1; also elsewhere on the board

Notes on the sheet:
It shall be possible to switch between a (screw driver) poti and the DAC.
Simple DAC for I2C programming.
Light sensor TSL2561 for feedback.
This connector connects the driver to the LEDs.
32 x 2 = 64 stages. 1 stage consists out of 4 LEDs.

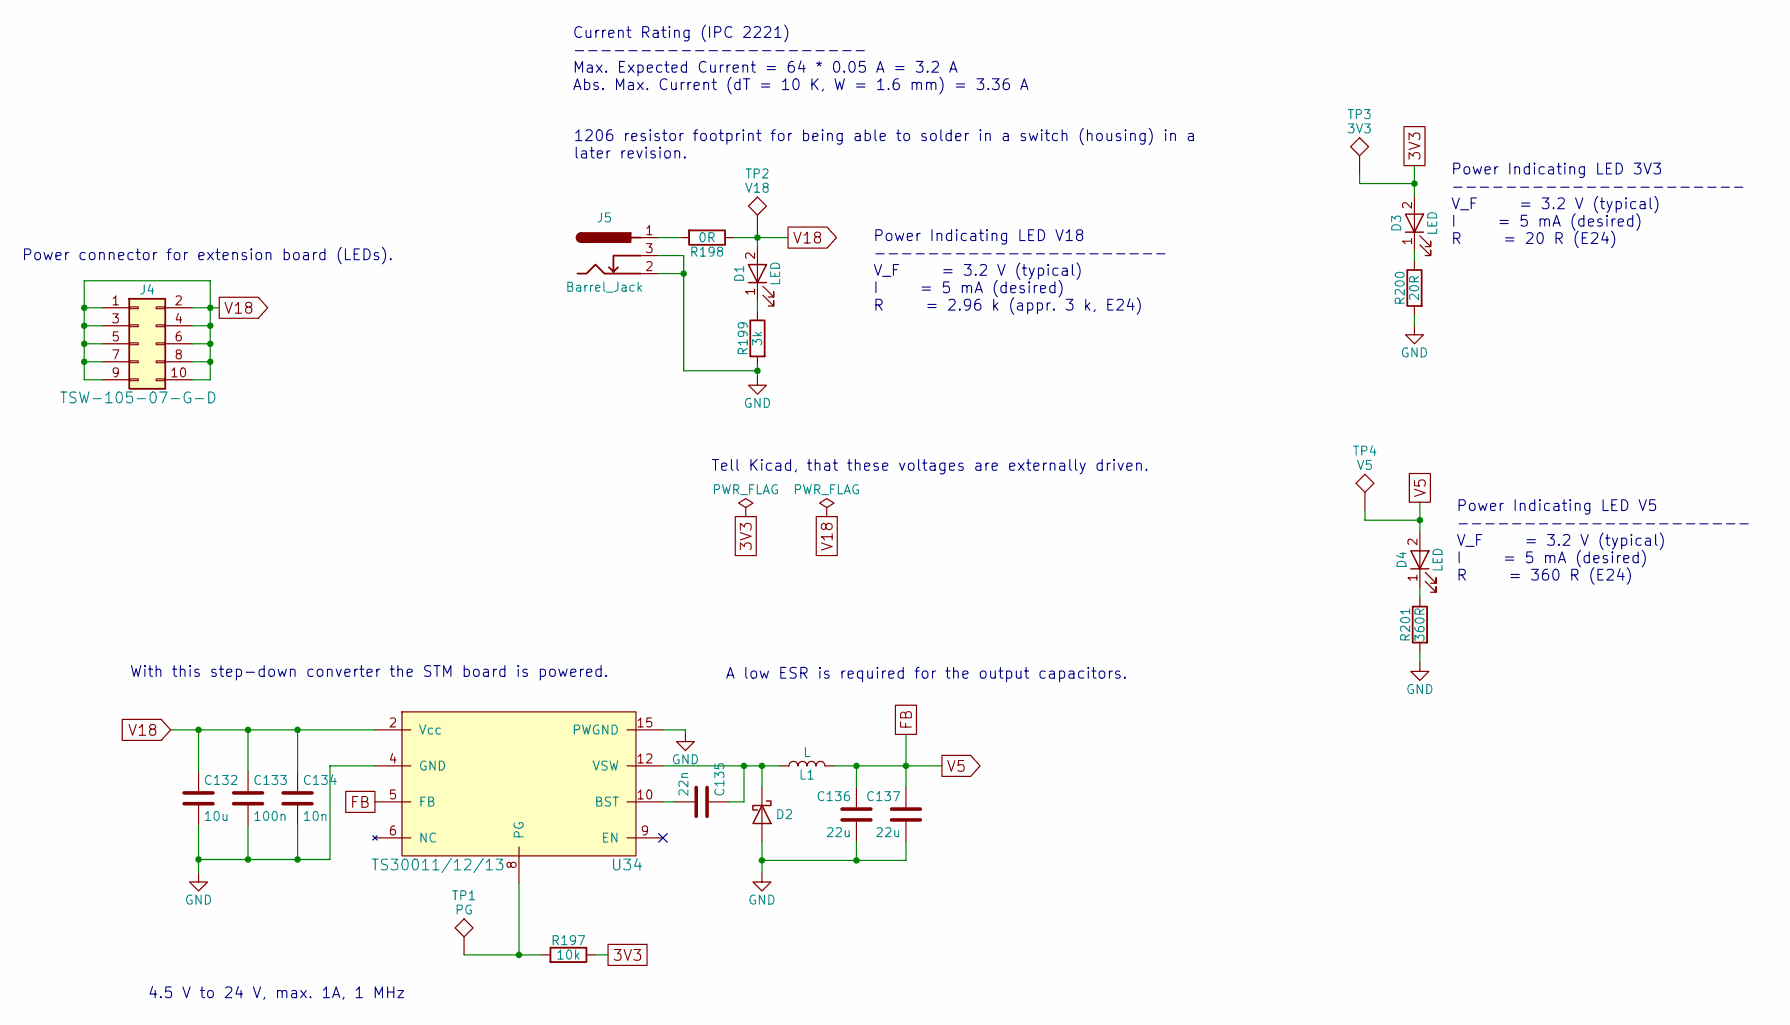
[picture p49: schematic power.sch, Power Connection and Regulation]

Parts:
C132: 10u; R_0603; Digikey 490-6403-6-ND
C133: 100n; R_0603; Digikey 311-1088-1-ND
C134: 10n; R_0603; Digikey 311-1085-1-ND
C135: 22n; R_0603; Digikey 1276-1104-1-ND
C136, C137: 22u; R_0603; Digikey 1276-2412-1-ND
D1, D3, D4: LED; LED_0603; Digikey 732-4971-1-ND
D2: D_Schottky; D_SOD-123; Digikey 1727-7332-1-ND
J4: Conn_02x05_Odd_Even; Pin_Header_Straight_2x05_Pitch2.54mm
J5: Barrel_Jack; BARREL_JACK
L1: L; WE-PD2-SMD-Power-Inductor; Digikey 732-1316-1-ND
R197: 10k; R_0603; Digikey 311-10KGRCT-ND
R198: 0R; R_1206; Digikey 311-0.0ERCT-ND
R199: 3k; R_0603; Digikey 311-3.0KGRCT-ND
R200: 20R; R_0603; Digikey 311-20GRCT-ND
R201: 360R; R_0603; Digikey 311-20GRCT-ND
TP1: PG; TP_SMD_quadr_1mm
TP2: V18; TP_SMD_quadr_1mm
TP3: 3V3; TP_SMD_quadr_1mm
TP4: V5; TP_SMD_quadr_1mm
U34: TS30011/12/13; QFN-16-1EP_3x3mm_Pitch0.5mm; Digikey TS30011-M050QFNRCT-ND

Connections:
+3V3: D3.2 (A), R197.1, TP3.1; also elsewhere on the board
E5V: C136.1, C137.1, D4.2 (A), L1.2, TP4.1, U34.5 (FB); also elsewhere on the board
GND: C132.2, C133.2, C134.2, C136.2, C137.2, D2.2 (A), J5.2, J5.3, R199.2, R200.2, R201.2, U34.4 (GND), U34.14 (PWGND), U34.15 (PWGND), U34.17 (Pad); also elsewhere on the board
unnamed: C135.1, D2.1 (K), L1.1, U34.1 (VSW), U34.12 (VSW), U34.13 (VSW), U34.16 (VSW)
unnamed: C135.2, U34.10 (BST)
unnamed: D1.1 (K), R199.1
unnamed: D3.1 (K), R200.1
unnamed: D4.1 (K), R201.1
unnamed: J5.1, R198.2
unnamed: R197.2, TP1.1, U34.8 (PG)
V18: C132.1, C133.1, C134.1, D1.2 (A), J4.1, J4.2, J4.3, J4.4, J4.5, J4.6, J4.7, J4.8, J4.9, J4.10, R198.1, TP2.1, U34.2 (Vcc), U34.3 (Vcc), U34.11 (Vcc); also elsewhere on the board

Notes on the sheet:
Power Indicating LED V18 ---------------------- V_F = 3.2 V (typical) I = 5 mA (desired) R = 2.96 k (appr. 3 k, E24)
A low ESR is required for the output capacitors.
Power Indicating LED V5 ---------------------- V_F = 3.2 V (typical) I = 5 mA (desired) R = 360 R (E24)
1206 resistor footprint for being able to solder in a switch (housing) in a later revision.
Power connector for extension board (LEDs).
With this step-down converter the STM board is powered.
Power Indicating LED 3V3 ---------------------- V_F = 3.2 V (typical) I = 5 mA (desired) R = 20 R (E24)
Tell Kicad, that these voltages are externally driven.
Current Rating (IPC 2221) ---------------------- Max. Expected Current = 64 * 0.05 A = 3.2 A Abs. Max. Current (dT = 10 K, W = 1.6 mm) = 3.36 A
4.5 V to 24 V, max. 1A, 1 MHz

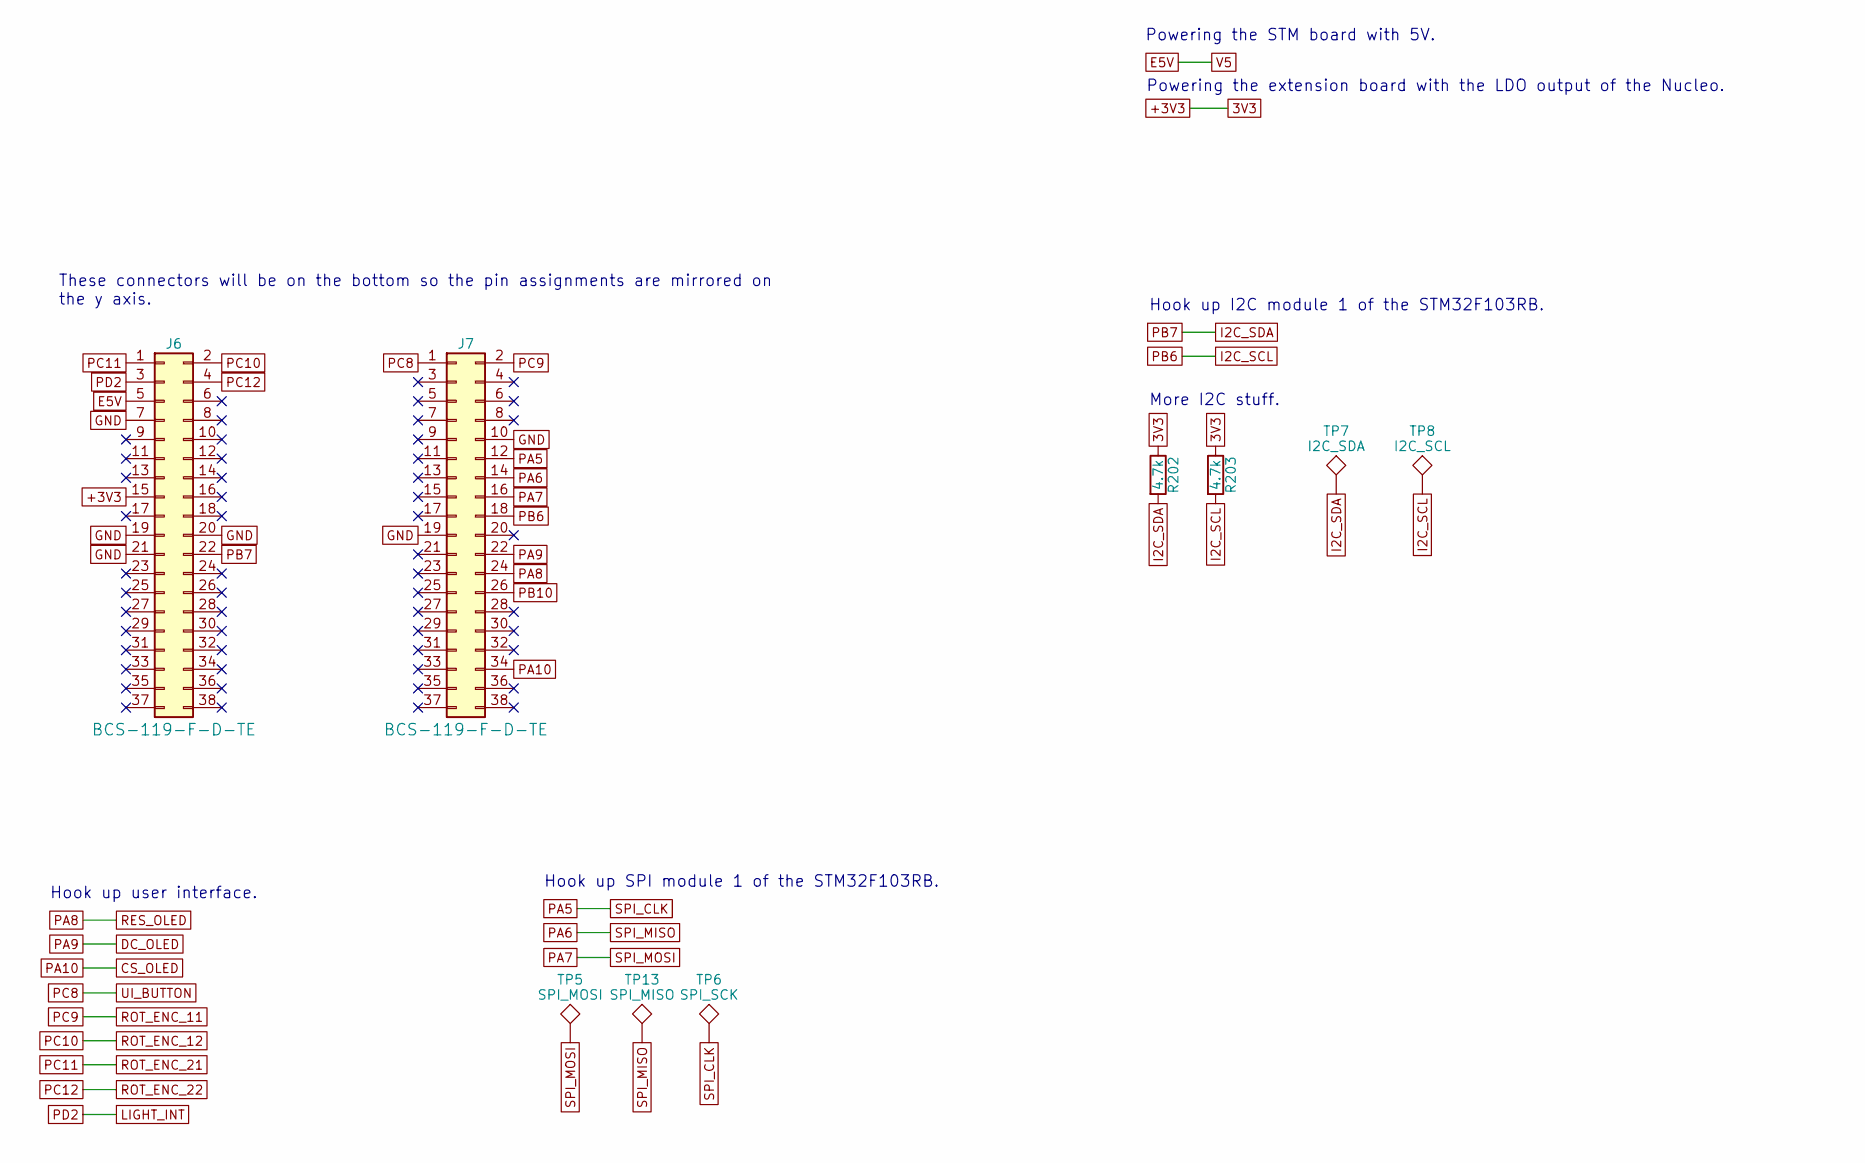
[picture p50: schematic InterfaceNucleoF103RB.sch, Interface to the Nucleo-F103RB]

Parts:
J6, J7: Conn_02x19_Odd_Even; Pin_Header_Straight_2x19_Pitch2.54mm
R202, R203: 4.7k; R_0603; Digikey 311-4.70KHRCT-ND
TP5: SPI_MOSI; TP_SMD_quadr_1mm
TP6: SPI_SCK; TP_SMD_quadr_1mm
TP7: I2C_SDA; TP_SMD_quadr_1mm
TP8: I2C_SCL; TP_SMD_quadr_1mm
TP13: SPI_MISO; TP_SMD_quadr_1mm

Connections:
+3V3: J6.15, R202.1, R203.1; also elsewhere on the board
CS_OLED: J7.34; also elsewhere on the board
DC_OLED: J7.22; also elsewhere on the board
E5V: J6.5; also elsewhere on the board
GND: J6.7, J6.19, J6.20, J6.21, J7.10, J7.19; also elsewhere on the board
I2C_SCL: J7.18, R203.2, TP8.1; also elsewhere on the board
I2C_SDA: J6.22, R202.2, TP7.1; also elsewhere on the board
LIGHT_INT: J6.3; also elsewhere on the board
PA5: J7.12, TP6.1; also elsewhere on the board
PA6: J7.14, TP13.1; also elsewhere on the board
PA7: J7.16, TP5.1; also elsewhere on the board
PA8: J7.24; also elsewhere on the board
PB10: J7.26; also elsewhere on the board
PC8: J7.1; also elsewhere on the board
PC9: J7.2; also elsewhere on the board
PC10: J6.2; also elsewhere on the board
PC11: J6.1; also elsewhere on the board
PC12: J6.4; also elsewhere on the board

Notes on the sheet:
These connectors will be on the bottom so the pin assignments are mirrored on the y axis.
Powering the STM board with 5V.
Hook up I2C module 1 of the STM32F103RB.
More I2C stuff.
Powering the extension board with the LDO output of the Nucleo.
Hook up SPI module 1 of the STM32F103RB.
Hook up user interface.

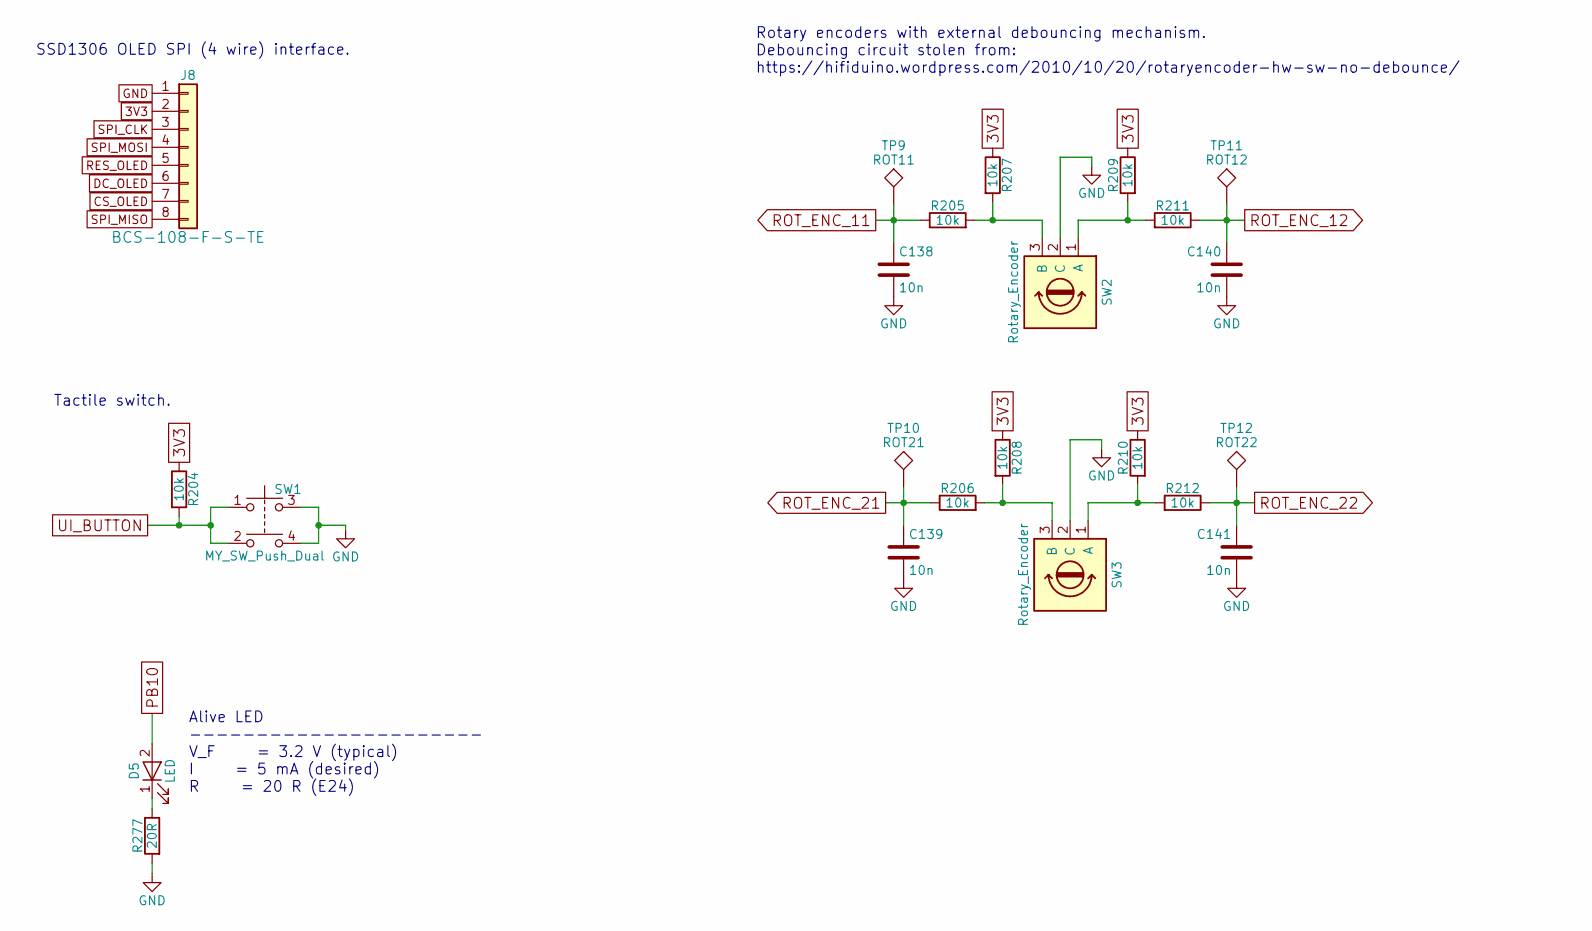
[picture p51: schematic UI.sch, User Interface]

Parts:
C138, C139, C140, C141: 10n; R_0603; Digikey 311-1085-1-ND
D5: LED; LED_0603; Digikey 732-4971-1-ND
J8: Conn_01x08; Pin_Header_Straight_1x08_Pitch2.54mm
R204, R205, R206, R207, R208, R209, R210, R211, R212: 10k; R_0603; Digikey 311-10KGRCT-ND
R277: 20R; R_0603; Digikey 1276-6153-1-ND
SW1: MY_SW_Push_Dual; SW_PUSH_TE_CONN_6x6; Digikey 450-1650-ND
SW2, SW3: Rotary_Encoder; ROT_ENC_EN12_TT_Electronics_No_Switch; Digikey 987-1399-ND
TP9: ROT11
TP10: ROT21
TP11: ROT12
TP12: ROT22

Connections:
+3V3: J8.2, R204.1, R207.1, R208.1, R209.1, R210.1; also elsewhere on the board
CS_OLED: J8.7; also elsewhere on the board
DC_OLED: J8.6; also elsewhere on the board
GND: C138.2, C139.2, C140.2, C141.2, J8.1, R277.2, SW1.3, SW1.4, SW2.2 (C), SW3.2 (C); also elsewhere on the board
unnamed: D5.1 (K), R277.1
unnamed: R205.2, R207.2, SW2.3 (B)
unnamed: R206.2, R208.2, SW3.3 (B)
unnamed: R209.2, R211.2, SW2.1 (A)
unnamed: R210.2, R212.2, SW3.1 (A)
PA5: J8.3; also elsewhere on the board
PA6: J8.8; also elsewhere on the board
PA7: J8.4; also elsewhere on the board
PA8: J8.5; also elsewhere on the board
PB10: D5.2 (A); also elsewhere on the board
PC8: R204.2, SW1.1, SW1.2; also elsewhere on the board
PC9: C138.1, R205.1, TP9.1; also elsewhere on the board
PC10: C140.1, R211.1, TP11.1; also elsewhere on the board
PC11: C139.1, R206.1, TP10.1; also elsewhere on the board
PC12: C141.1, R212.1, TP12.1; also elsewhere on the board

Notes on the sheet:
SSD1306 OLED SPI (4 wire) interface.
Rotary encoders with external debouncing mechanism. Debouncing circuit stolen from: https://hifiduino.wordpress.com/2010/10/20/rotaryencoder-hw-sw-no-debounce/
Tactile switch.
Alive LED ---------------------- V_F = 3.2 V (typical) I = 5 mA (desired) R = 20 R (E24)

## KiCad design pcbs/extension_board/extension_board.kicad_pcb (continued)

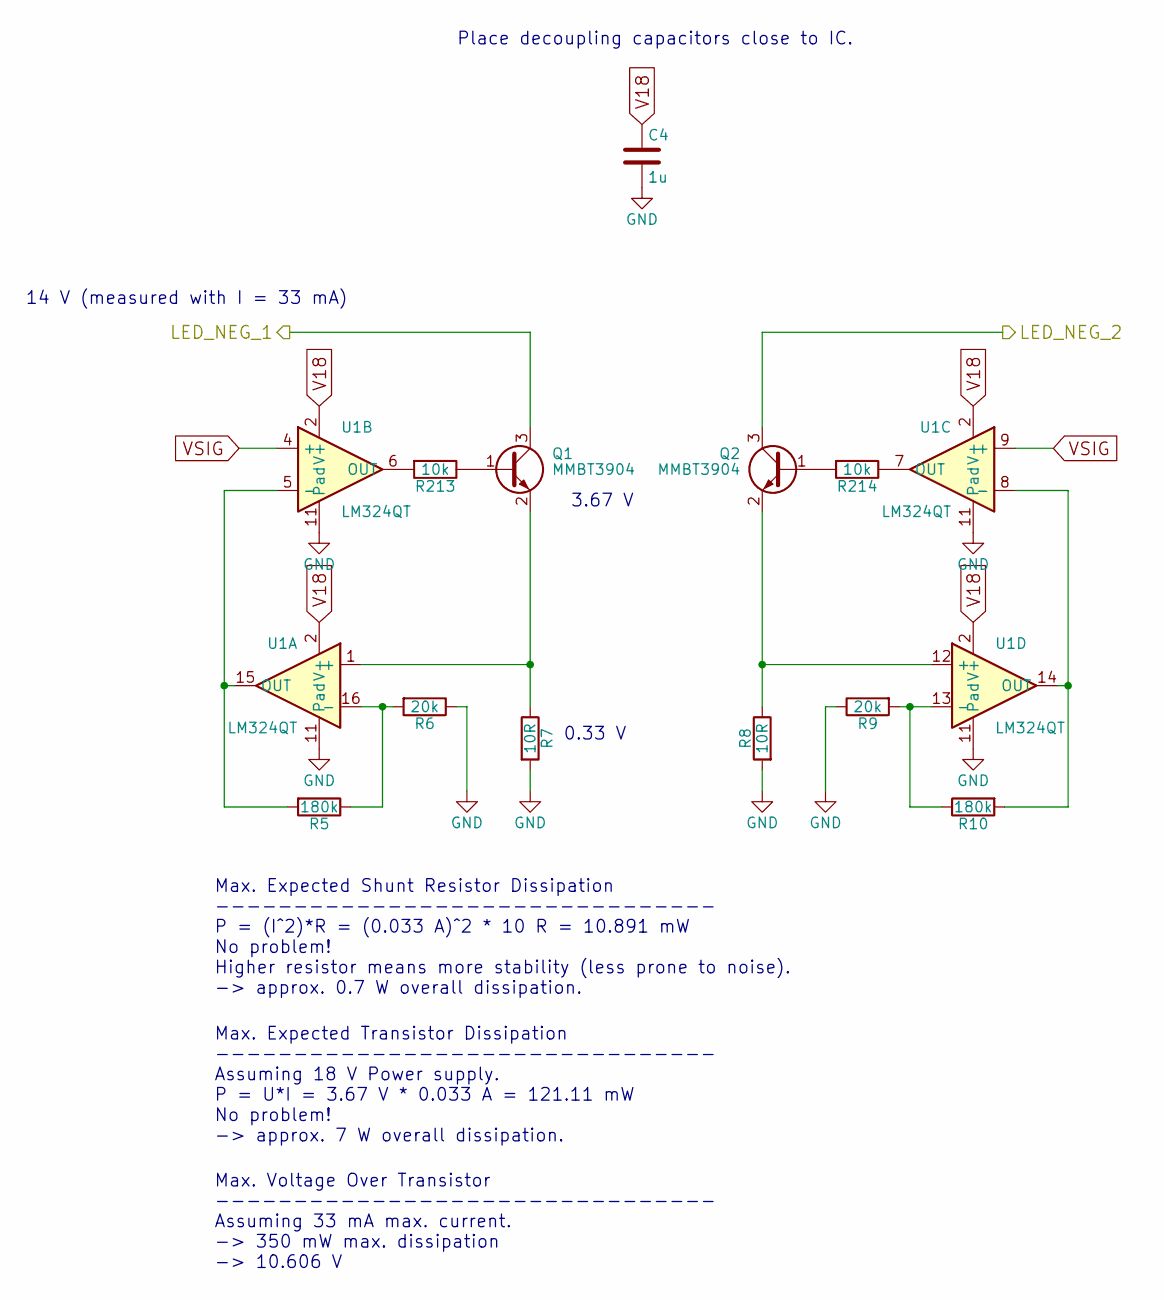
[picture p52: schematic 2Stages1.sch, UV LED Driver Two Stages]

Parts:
C4: 1u; R_0603; Digikey 399-3118-1-ND
Q1, Q2: MMBT3904; SOT-23; Digikey MMBT3904TPMSCT-ND
R5, R10: 180k; R_0603; Digikey 311-180KHRCT-ND
R6, R9: 20k; R_0603; Digikey 311-20.0KHRCT-ND
R7, R8: 10R; R_0603; Digikey 311-10.0HRCT-ND
R213, R214: 10k; R_0603; Digikey 311-10KGRCT-ND
U1: LM324QT; QFN-16-1EP_3x3mm_Pitch0.5mm; Digikey 497-12005-1-ND

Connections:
GND: C4.2, R6.1, R7.2, R8.2, R9.1, U1.11 (Pad), U1.17 (Pad); also elsewhere on the board
LED_N_01: Q1.3 (C); also elsewhere on the board
LED_N_02: Q2.3 (C); also elsewhere on the board
unnamed: Q1.1 (B), R213.1
unnamed: Q1.2 (E), R7.1, U1.1 (+)
unnamed: Q2.1 (B), R214.2
unnamed: Q2.2 (E), R8.1, U1.12 (+)
unnamed: R5.1, R6.2, U1.16 (-)
unnamed: R5.2, U1.5 (-), U1.15 (OUT)
unnamed: R9.2, R10.1, U1.13 (-)
unnamed: R10.2, U1.8 (-), U1.14 (OUT)
unnamed: R213.2, U1.6 (OUT)
unnamed: R214.1, U1.7 (OUT)
V18: C4.1, U1.2 (V+); also elsewhere on the board
VSIG: U1.4 (+), U1.9 (+); also elsewhere on the board

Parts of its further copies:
C8, C12, C16, C20, C24, C28, C32, C36, C40, C44, C48, C52, C56, C60, C64, C68, C72, C76, C80, C84, C88, C92, C96, C100, C104, C108, C112, C116, C120, C124, C128: 1u; R_0603; Digikey 399-3118-1-ND
Q3, Q4, Q5, Q6, Q7, Q8, Q9, Q10, Q11, Q12, Q13, Q14, Q15, Q16, Q17, Q18, Q19, Q20, Q21, Q22, Q23, Q24, Q25, Q26, Q27, Q28, Q29, Q30, Q31, Q32, Q33, Q34, Q35, Q36, Q37, Q38, Q39, Q40, Q41, Q42, Q43, Q44, Q45, Q46, Q47, Q48, Q49, Q50, Q51, Q52, Q53, Q54, Q55, Q56, Q57, Q58, Q59, Q60, Q61, Q62, Q63, Q64: MMBT3904; SOT-23; Digikey MMBT3904TPMSCT-ND
R11, R16, R17, R22, R23, R28, R29, R34, R35, R40, R41, R46, R47, R52, R53, R58, R59, R64, R65, R70, R71, R76, R77, R82, R83, R88, R89, R94, R95, R100, R101, R106, R107, R112, R113, R118, R119, R124, R125, R130, R131, R136, R137, R142, R143, R148, R149, R154, R155, R160, R161, R166, R167, R172, R173, R178, R179, R184, R185, R190, R191, R196: 180k; R_0603; Digikey 311-180KHRCT-ND
R12, R15, R18, R21, R24, R27, R30, R33, R36, R39, R42, R45, R48, R51, R54, R57, R60, R63, R66, R69, R72, R75, R78, R81, R84, R87, R90, R93, R96, R99, R102, R105, R108, R111, R114, R117, R120, R123, R126, R129, R132, R135, R138, R141, R144, R147, R150, R153, R156, R159, R162, R165, R168, R171, R174, R177, R180, R183, R186, R189, R192, R195: 20k; R_0603; Digikey 311-20.0KHRCT-ND
R13, R14, R19, R20, R25, R26, R31, R32, R37, R38, R43, R44, R49, R50, R55, R56, R61, R62, R67, R68, R73, R74, R79, R80, R85, R86, R91, R92, R97, R98, R103, R104, R109, R110, R115, R116, R121, R122, R127, R128, R133, R134, R139, R140, R145, R146, R151, R152, R157, R158, R163, R164, R169, R170, R175, R176, R181, R182, R187, R188, R193, R194: 10R; R_0603; Digikey 311-10.0HRCT-ND
R215, R216, R217, R218, R219, R220, R221, R222, R223, R224, R225, R226, R227, R228, R229, R230, R231, R232, R233, R234, R235, R236, R237, R238, R239, R240, R241, R242, R243, R244, R245, R246, R247, R248, R249, R250, R251, R252, R253, R254, R255, R256, R257, R258, R259, R260, R261, R262, R263, R264, R265, R266, R267, R268, R269, R270, R271, R272, R273, R274, R275, R276: 10k; R_0603; Digikey 311-10KGRCT-ND
U2, U3, U4, U5, U6, U7, U8, U9, U10, U11, U12, U13, U14, U15, U16, U17, U18, U19, U20, U21, U22, U23, U24, U25, U26, U27, U28, U29, U30, U31, U32: LM324QT; QFN-16-1EP_3x3mm_Pitch0.5mm; Digikey 497-12005-1-ND

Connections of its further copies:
GND: C8.2, C12.2, C16.2, C20.2, C24.2, C28.2, C32.2, C36.2, C40.2, C44.2, C48.2, C52.2, C56.2, C60.2, C64.2, C68.2, C72.2, C76.2, C80.2, C84.2, C88.2, C92.2, C96.2, C100.2, C104.2, C108.2, C112.2, C116.2, C120.2, C124.2, C128.2, R12.1, R13.2, R14.2, R15.1, R18.1, R19.2, R20.2, R21.1, R24.1, R25.2, R26.2, R27.1, R30.1, R31.2, R32.2, R33.1, R36.1, R37.2, R38.2, R39.1, R42.1, R43.2, R44.2, R45.1, R48.1, R49.2, R50.2, R51.1, R54.1, R55.2, R56.2, R57.1, R60.1, R61.2, R62.2, R63.1, R66.1, R67.2, R68.2, R69.1, R72.1, R73.2, R74.2, R75.1, R78.1, R79.2, R80.2, R81.1, R84.1, R85.2, R86.2, R87.1, R90.1, R91.2, R92.2, R93.1, R96.1, R97.2, R98.2, R99.1, R102.1, R103.2, R104.2, R105.1, R108.1, R109.2, R110.2, R111.1, R114.1, R115.2, R116.2, R117.1, R120.1, R121.2, R122.2, R123.1, R126.1, R127.2, R128.2, R129.1, R132.1, R133.2, R134.2, R135.1, R138.1, R139.2, R140.2, R141.1, R144.1, R145.2, R146.2, R147.1, R150.1, R151.2, R152.2, R153.1, R156.1, R157.2, R158.2, R159.1, R162.1, R163.2, R164.2, R165.1, R168.1, R169.2, R170.2, R171.1, R174.1, R175.2, R176.2, R177.1, R180.1, R181.2, R182.2, R183.1, R186.1, R187.2, R188.2, R189.1, R192.1, R193.2, R194.2, R195.1, U2.11 (Pad), U2.17 (Pad), U3.11 (Pad), U3.17 (Pad), U4.11 (Pad), U4.17 (Pad), U5.11 (Pad), U5.17 (Pad), U6.11 (Pad), U6.17 (Pad), U7.11 (Pad), U7.17 (Pad), U8.11 (Pad), U8.17 (Pad), U9.11 (Pad), U9.17 (Pad), U10.11 (Pad), U10.17 (Pad), U11.11 (Pad), U11.17 (Pad), U12.11 (Pad), U12.17 (Pad), U13.11 (Pad), U13.17 (Pad), U14.11 (Pad), U14.17 (Pad), U15.11 (Pad), U15.17 (Pad), U16.11 (Pad), U16.17 (Pad), U17.11 (Pad), U17.17 (Pad), U18.11 (Pad), U18.17 (Pad), U19.11 (Pad), U19.17 (Pad), U20.11 (Pad), U20.17 (Pad), U21.11 (Pad), U21.17 (Pad), U22.11 (Pad), U22.17 (Pad), U23.11 (Pad), U23.17 (Pad), U24.11 (Pad), U24.17 (Pad), U25.11 (Pad), U25.17 (Pad), U26.11 (Pad), U26.17 (Pad), U27.11 (Pad), U27.17 (Pad), U28.11 (Pad), U28.17 (Pad), U29.11 (Pad), U29.17 (Pad), U30.11 (Pad), U30.17 (Pad), U31.11 (Pad), U31.17 (Pad), U32.11 (Pad), U32.17 (Pad); also elsewhere on the board
LED_N_03: Q3.3 (C); also elsewhere on the board
LED_N_04: Q4.3 (C); also elsewhere on the board
LED_N_05: Q5.3 (C); also elsewhere on the board
LED_N_06: Q6.3 (C); also elsewhere on the board
LED_N_07: Q7.3 (C); also elsewhere on the board
LED_N_08: Q8.3 (C); also elsewhere on the board
LED_N_09: Q9.3 (C); also elsewhere on the board
LED_N_10: Q10.3 (C); also elsewhere on the board
LED_N_11: Q11.3 (C); also elsewhere on the board
LED_N_12: Q12.3 (C); also elsewhere on the board
LED_N_13: Q13.3 (C); also elsewhere on the board
LED_N_14: Q14.3 (C); also elsewhere on the board
LED_N_15: Q15.3 (C); also elsewhere on the board
LED_N_16: Q16.3 (C); also elsewhere on the board
LED_N_17: Q17.3 (C); also elsewhere on the board
LED_N_18: Q18.3 (C); also elsewhere on the board
LED_N_19: Q19.3 (C); also elsewhere on the board
LED_N_20: Q20.3 (C); also elsewhere on the board
LED_N_21: Q21.3 (C); also elsewhere on the board
LED_N_22: Q22.3 (C); also elsewhere on the board
LED_N_23: Q23.3 (C); also elsewhere on the board
LED_N_24: Q24.3 (C); also elsewhere on the board
LED_N_25: Q25.3 (C); also elsewhere on the board
LED_N_26: Q26.3 (C); also elsewhere on the board
LED_N_27: Q27.3 (C); also elsewhere on the board
LED_N_28: Q28.3 (C); also elsewhere on the board
LED_N_29: Q29.3 (C); also elsewhere on the board
LED_N_30: Q30.3 (C); also elsewhere on the board
LED_N_31: Q31.3 (C); also elsewhere on the board
LED_N_32: Q32.3 (C); also elsewhere on the board
LED_N_33: Q34.3 (C); also elsewhere on the board
LED_N_34: Q33.3 (C); also elsewhere on the board
LED_N_35: Q36.3 (C); also elsewhere on the board
LED_N_36: Q35.3 (C); also elsewhere on the board
LED_N_37: Q38.3 (C); also elsewhere on the board
LED_N_38: Q37.3 (C); also elsewhere on the board
LED_N_39: Q40.3 (C); also elsewhere on the board
LED_N_40: Q39.3 (C); also elsewhere on the board
LED_N_41: Q42.3 (C); also elsewhere on the board
LED_N_42: Q41.3 (C); also elsewhere on the board
LED_N_43: Q44.3 (C); also elsewhere on the board
LED_N_44: Q43.3 (C); also elsewhere on the board
LED_N_45: Q46.3 (C); also elsewhere on the board
LED_N_46: Q45.3 (C); also elsewhere on the board
LED_N_47: Q48.3 (C); also elsewhere on the board
LED_N_48: Q47.3 (C); also elsewhere on the board
LED_N_49: Q50.3 (C); also elsewhere on the board
LED_N_50: Q49.3 (C); also elsewhere on the board
LED_N_51: Q52.3 (C); also elsewhere on the board
LED_N_52: Q51.3 (C); also elsewhere on the board
LED_N_53: Q54.3 (C); also elsewhere on the board
LED_N_54: Q53.3 (C); also elsewhere on the board
LED_N_55: Q56.3 (C); also elsewhere on the board
LED_N_56: Q55.3 (C); also elsewhere on the board
LED_N_57: Q58.3 (C); also elsewhere on the board
LED_N_58: Q57.3 (C); also elsewhere on the board
LED_N_59: Q60.3 (C); also elsewhere on the board
LED_N_60: Q59.3 (C); also elsewhere on the board
LED_N_61: Q62.3 (C); also elsewhere on the board
LED_N_62: Q61.3 (C); also elsewhere on the board
LED_N_63: Q64.3 (C); also elsewhere on the board
LED_N_64: Q63.3 (C); also elsewhere on the board
unnamed: Q3.1 (B), R215.1
unnamed: Q3.2 (E), R13.1, U2.1 (+)
unnamed: Q4.1 (B), R216.2
unnamed: Q4.2 (E), R14.1, U2.12 (+)
unnamed: Q5.1 (B), R217.1
unnamed: Q5.2 (E), R19.1, U3.1 (+)
unnamed: Q6.1 (B), R218.2
unnamed: Q6.2 (E), R20.1, U3.12 (+)
unnamed: Q7.1 (B), R219.1
unnamed: Q7.2 (E), R25.1, U4.1 (+)
unnamed: Q8.1 (B), R220.2
unnamed: Q8.2 (E), R26.1, U4.12 (+)
unnamed: Q9.1 (B), R221.1
unnamed: Q9.2 (E), R31.1, U5.1 (+)
unnamed: Q10.1 (B), R222.2
unnamed: Q10.2 (E), R32.1, U5.12 (+)
unnamed: Q11.1 (B), R223.1
unnamed: Q11.2 (E), R37.1, U6.1 (+)
unnamed: Q12.1 (B), R224.2
unnamed: Q12.2 (E), R38.1, U6.12 (+)
unnamed: Q13.1 (B), R225.1
unnamed: Q13.2 (E), R43.1, U7.1 (+)
unnamed: Q14.1 (B), R226.2
unnamed: Q14.2 (E), R44.1, U7.12 (+)
unnamed: Q15.1 (B), R227.1
unnamed: Q15.2 (E), R49.1, U8.1 (+)
unnamed: Q16.1 (B), R228.2
unnamed: Q16.2 (E), R50.1, U8.12 (+)
unnamed: Q17.1 (B), R229.1
unnamed: Q17.2 (E), R55.1, U9.1 (+)
unnamed: Q18.1 (B), R230.2
unnamed: Q18.2 (E), R56.1, U9.12 (+)
unnamed: Q19.1 (B), R231.1
unnamed: Q19.2 (E), R61.1, U10.1 (+)
unnamed: Q20.1 (B), R232.2
unnamed: Q20.2 (E), R62.1, U10.12 (+)
unnamed: Q21.1 (B), R233.1
unnamed: Q21.2 (E), R67.1, U11.1 (+)
unnamed: Q22.1 (B), R234.2
unnamed: Q22.2 (E), R68.1, U11.12 (+)
unnamed: Q23.1 (B), R235.1
unnamed: Q23.2 (E), R73.1, U12.1 (+)
unnamed: Q24.1 (B), R236.2
unnamed: Q24.2 (E), R74.1, U12.12 (+)
unnamed: Q25.1 (B), R237.1
unnamed: Q25.2 (E), R79.1, U13.1 (+)
unnamed: Q26.1 (B), R238.2
unnamed: Q26.2 (E), R80.1, U13.12 (+)
unnamed: Q27.1 (B), R239.1
unnamed: Q27.2 (E), R85.1, U14.1 (+)
unnamed: Q28.1 (B), R240.2
unnamed: Q28.2 (E), R86.1, U14.12 (+)
unnamed: Q29.1 (B), R241.1
unnamed: Q29.2 (E), R91.1, U15.1 (+)
unnamed: Q30.1 (B), R242.2
unnamed: Q30.2 (E), R92.1, U15.12 (+)
unnamed: Q31.1 (B), R243.1
unnamed: Q31.2 (E), R97.1, U16.1 (+)
unnamed: Q32.1 (B), R244.2
unnamed: Q32.2 (E), R98.1, U16.12 (+)
unnamed: Q33.1 (B), R275.1
unnamed: Q33.2 (E), R193.1, U17.1 (+)
unnamed: Q34.1 (B), R276.2
unnamed: Q34.2 (E), R194.1, U17.12 (+)
unnamed: Q35.1 (B), R273.1
unnamed: Q35.2 (E), R187.1, U18.1 (+)
unnamed: Q36.1 (B), R274.2
unnamed: Q36.2 (E), R188.1, U18.12 (+)
unnamed: Q37.1 (B), R271.1
unnamed: Q37.2 (E), R181.1, U19.1 (+)
unnamed: Q38.1 (B), R272.2
unnamed: Q38.2 (E), R182.1, U19.12 (+)
unnamed: Q39.1 (B), R269.1
unnamed: Q39.2 (E), R175.1, U20.1 (+)
unnamed: Q40.1 (B), R270.2
unnamed: Q40.2 (E), R176.1, U20.12 (+)
unnamed: Q41.1 (B), R267.1
unnamed: Q41.2 (E), R169.1, U21.1 (+)
unnamed: Q42.1 (B), R268.2
unnamed: Q42.2 (E), R170.1, U21.12 (+)
unnamed: Q43.1 (B), R265.1
unnamed: Q43.2 (E), R163.1, U22.1 (+)
unnamed: Q44.1 (B), R266.2
unnamed: Q44.2 (E), R164.1, U22.12 (+)
unnamed: Q45.1 (B), R263.1
unnamed: Q45.2 (E), R157.1, U23.1 (+)
unnamed: Q46.1 (B), R264.2
unnamed: Q46.2 (E), R158.1, U23.12 (+)
unnamed: Q47.1 (B), R261.1
unnamed: Q47.2 (E), R151.1, U24.1 (+)
unnamed: Q48.1 (B), R262.2
unnamed: Q48.2 (E), R152.1, U24.12 (+)
unnamed: Q49.1 (B), R259.1
unnamed: Q49.2 (E), R145.1, U25.1 (+)
unnamed: Q50.1 (B), R260.2
unnamed: Q50.2 (E), R146.1, U25.12 (+)
unnamed: Q51.1 (B), R257.1
unnamed: Q51.2 (E), R139.1, U26.1 (+)
unnamed: Q52.1 (B), R258.2
unnamed: Q52.2 (E), R140.1, U26.12 (+)
unnamed: Q53.1 (B), R255.1
unnamed: Q53.2 (E), R133.1, U27.1 (+)
unnamed: Q54.1 (B), R256.2
unnamed: Q54.2 (E), R134.1, U27.12 (+)
unnamed: Q55.1 (B), R253.1
unnamed: Q55.2 (E), R127.1, U28.1 (+)
unnamed: Q56.1 (B), R254.2
unnamed: Q56.2 (E), R128.1, U28.12 (+)
unnamed: Q57.1 (B), R251.1
unnamed: Q57.2 (E), R121.1, U29.1 (+)
unnamed: Q58.1 (B), R252.2
unnamed: Q58.2 (E), R122.1, U29.12 (+)
unnamed: Q59.1 (B), R249.1
unnamed: Q59.2 (E), R115.1, U30.1 (+)
unnamed: Q60.1 (B), R250.2
unnamed: Q60.2 (E), R116.1, U30.12 (+)
unnamed: Q61.1 (B), R247.1
unnamed: Q61.2 (E), R109.1, U31.1 (+)
unnamed: Q62.1 (B), R248.2
unnamed: Q62.2 (E), R110.1, U31.12 (+)
unnamed: Q63.1 (B), R245.1
unnamed: Q63.2 (E), R103.1, U32.1 (+)
unnamed: Q64.1 (B), R246.2
unnamed: Q64.2 (E), R104.1, U32.12 (+)
unnamed: R11.1, R12.2, U2.16 (-)
unnamed: R11.2, U2.5 (-), U2.15 (OUT)
unnamed: R15.2, R16.1, U2.13 (-)
unnamed: R16.2, U2.8 (-), U2.14 (OUT)
unnamed: R17.1, R18.2, U3.16 (-)
unnamed: R17.2, U3.5 (-), U3.15 (OUT)
unnamed: R21.2, R22.1, U3.13 (-)
unnamed: R22.2, U3.8 (-), U3.14 (OUT)
unnamed: R23.1, R24.2, U4.16 (-)
unnamed: R23.2, U4.5 (-), U4.15 (OUT)
unnamed: R27.2, R28.1, U4.13 (-)
unnamed: R28.2, U4.8 (-), U4.14 (OUT)
unnamed: R29.1, R30.2, U5.16 (-)
unnamed: R29.2, U5.5 (-), U5.15 (OUT)
unnamed: R33.2, R34.1, U5.13 (-)
unnamed: R34.2, U5.8 (-), U5.14 (OUT)
unnamed: R35.1, R36.2, U6.16 (-)
unnamed: R35.2, U6.5 (-), U6.15 (OUT)
unnamed: R39.2, R40.1, U6.13 (-)
unnamed: R40.2, U6.8 (-), U6.14 (OUT)
unnamed: R41.1, R42.2, U7.16 (-)
unnamed: R41.2, U7.5 (-), U7.15 (OUT)
unnamed: R45.2, R46.1, U7.13 (-)
unnamed: R46.2, U7.8 (-), U7.14 (OUT)
unnamed: R47.1, R48.2, U8.16 (-)
unnamed: R47.2, U8.5 (-), U8.15 (OUT)
unnamed: R51.2, R52.1, U8.13 (-)
unnamed: R52.2, U8.8 (-), U8.14 (OUT)
unnamed: R53.1, R54.2, U9.16 (-)
unnamed: R53.2, U9.5 (-), U9.15 (OUT)
unnamed: R57.2, R58.1, U9.13 (-)
unnamed: R58.2, U9.8 (-), U9.14 (OUT)
unnamed: R59.1, R60.2, U10.16 (-)
unnamed: R59.2, U10.5 (-), U10.15 (OUT)
unnamed: R63.2, R64.1, U10.13 (-)
unnamed: R64.2, U10.8 (-), U10.14 (OUT)
unnamed: R65.1, R66.2, U11.16 (-)
unnamed: R65.2, U11.5 (-), U11.15 (OUT)
unnamed: R69.2, R70.1, U11.13 (-)
unnamed: R70.2, U11.8 (-), U11.14 (OUT)
unnamed: R71.1, R72.2, U12.16 (-)
unnamed: R71.2, U12.5 (-), U12.15 (OUT)
unnamed: R75.2, R76.1, U12.13 (-)
unnamed: R76.2, U12.8 (-), U12.14 (OUT)
unnamed: R77.1, R78.2, U13.16 (-)
unnamed: R77.2, U13.5 (-), U13.15 (OUT)
unnamed: R81.2, R82.1, U13.13 (-)
unnamed: R82.2, U13.8 (-), U13.14 (OUT)
unnamed: R83.1, R84.2, U14.16 (-)
unnamed: R83.2, U14.5 (-), U14.15 (OUT)
unnamed: R87.2, R88.1, U14.13 (-)
unnamed: R88.2, U14.8 (-), U14.14 (OUT)
unnamed: R89.1, R90.2, U15.16 (-)
unnamed: R89.2, U15.5 (-), U15.15 (OUT)
unnamed: R93.2, R94.1, U15.13 (-)
unnamed: R94.2, U15.8 (-), U15.14 (OUT)
unnamed: R95.1, R96.2, U16.16 (-)
unnamed: R95.2, U16.5 (-), U16.15 (OUT)
unnamed: R99.2, R100.1, U16.13 (-)
unnamed: R100.2, U16.8 (-), U16.14 (OUT)
unnamed: R101.1, R102.2, U32.16 (-)
unnamed: R101.2, U32.5 (-), U32.15 (OUT)
unnamed: R105.2, R106.1, U32.13 (-)
unnamed: R106.2, U32.8 (-), U32.14 (OUT)
unnamed: R107.1, R108.2, U31.16 (-)
unnamed: R107.2, U31.5 (-), U31.15 (OUT)
unnamed: R111.2, R112.1, U31.13 (-)
unnamed: R112.2, U31.8 (-), U31.14 (OUT)
unnamed: R113.1, R114.2, U30.16 (-)
unnamed: R113.2, U30.5 (-), U30.15 (OUT)
unnamed: R117.2, R118.1, U30.13 (-)
unnamed: R118.2, U30.8 (-), U30.14 (OUT)
unnamed: R119.1, R120.2, U29.16 (-)
unnamed: R119.2, U29.5 (-), U29.15 (OUT)
unnamed: R123.2, R124.1, U29.13 (-)
unnamed: R124.2, U29.8 (-), U29.14 (OUT)
unnamed: R125.1, R126.2, U28.16 (-)
unnamed: R125.2, U28.5 (-), U28.15 (OUT)
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

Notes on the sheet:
Place decoupling capacitors close to IC.
Max. Expected Shunt Resistor Dissipation -------------------------------- P = (I^2)*R = (0.033 A)^2 * 10 R = 10.891 mW No problem! Higher resistor means more stability (less prone to noise). -> approx. 0.7 W overall dissipation.
14 V (measured with I = 33 mA)
0.33 V
3.67 V
Max. Expected Transistor Dissipation -------------------------------- Assuming 18 V Power supply. P = U*I = 3.67 V * 0.033 A = 121.11 mW No problem! -> approx. 7 W overall dissipation.
Max. Voltage Over Transistor -------------------------------- Assuming 33 mA max. current. -> 350 mW max. dissipation -> 10.606 V

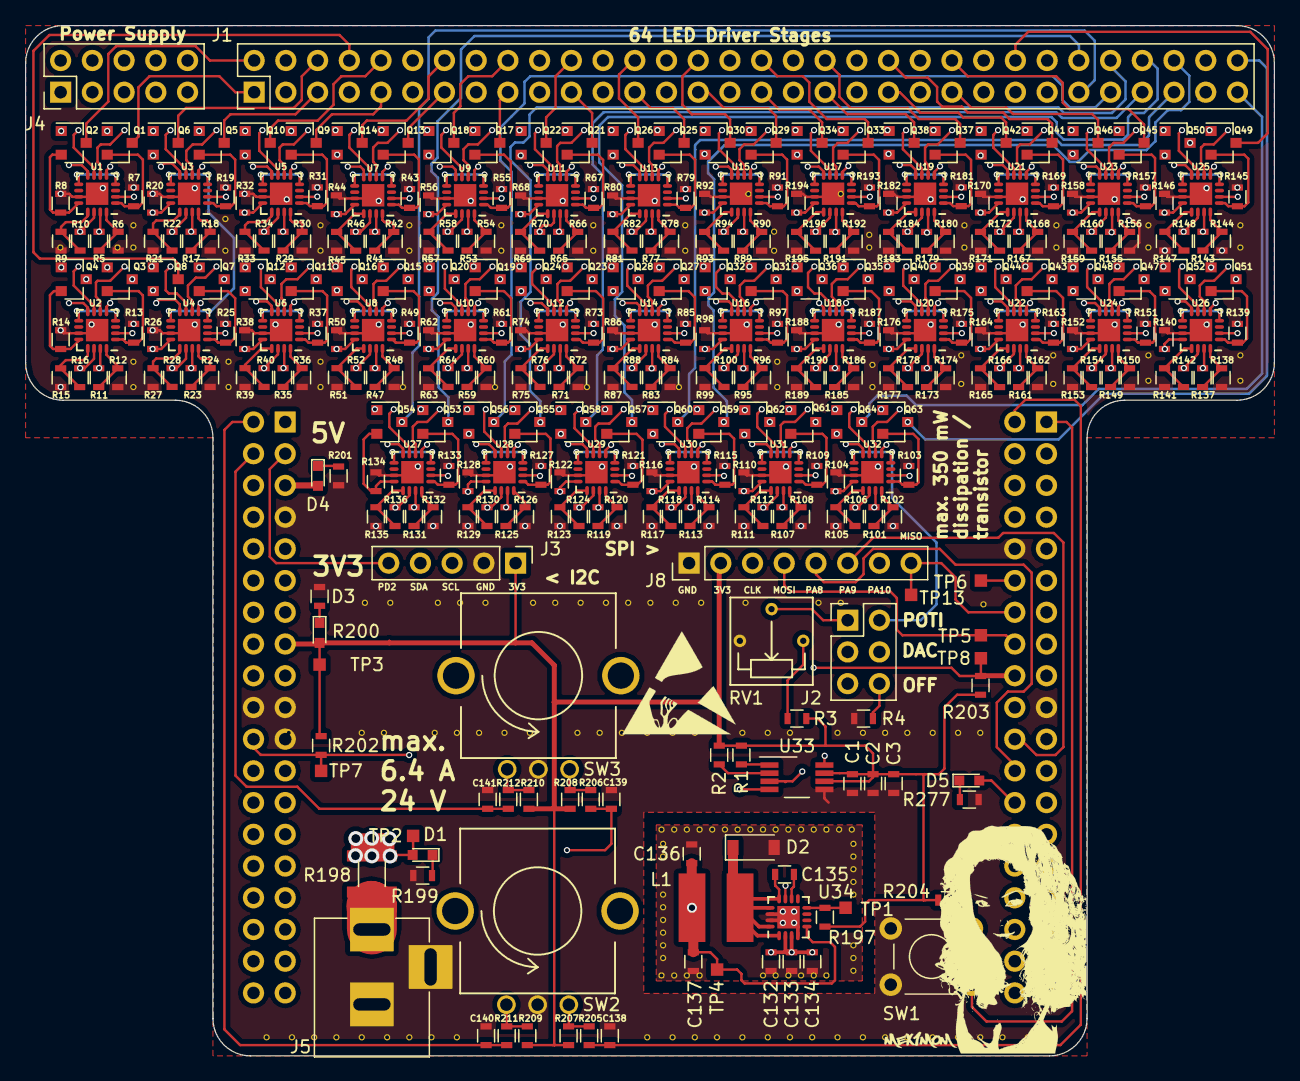
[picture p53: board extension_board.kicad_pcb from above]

Board: 4 copper layers, 100.0 x 82.5 mm, 447 parts (0 on the bottom side), 421 nets.

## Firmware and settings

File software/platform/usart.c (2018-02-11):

/*
 * usart.c
 *
 *  Created on: Dec 6, 2017
 *      Author: maximilian
 */

#include "usart.h"
#include "../os/queues.h"
#include "stm32f10x_gpio.h"
#include "stm32f10x_usart.h"
#include "../os/error.h"

static uint8_t tx_overflow = 0;

static osQUEUE_t usart_rx_q, usart_tx_q;

static uint8_t usart_rx_data[USART_QUEUE_SIZE];
static uint8_t usart_tx_data[USART_QUEUE_SIZE];

void usart2Init(void)
{
	/* Enable clocks. */
	RCC_APB2PeriphClockCmd(RCC_APB2Periph_AFIO | RCC_APB2Periph_GPIOA , ENABLE);
	RCC_APB1PeriphClockCmd(RCC_APB1Periph_USART2, ENABLE);

	/* Initialize used GPIOs. */
	GPIO_InitTypeDef GPIO_InitStruct;
	GPIO_StructInit(&GPIO_InitStruct);

	/* Initialize USART2_TX */
	GPIO_InitStruct.GPIO_Pin = GPIO_Pin_2;
	GPIO_InitStruct.GPIO_Speed = GPIO_Speed_50MHz;
	GPIO_InitStruct.GPIO_Mode = GPIO_Mode_AF_PP;
	GPIO_Init(GPIOA, &GPIO_InitStruct);

	/* Init. USART2_RX */
	GPIO_InitStruct.GPIO_Pin = GPIO_Pin_3;
	GPIO_InitStruct.GPIO_Speed = GPIO_Speed_50MHz;
	GPIO_InitStruct.GPIO_Mode = GPIO_Mode_IN_FLOATING;
	GPIO_Init(GPIOA, &GPIO_InitStruct);

	/* Init. USART2 peripheral. */
	USART_InitTypeDef USART_InitStructure ;
	USART_StructInit(&USART_InitStructure );
	USART_InitStructure.USART_BaudRate = 9600;
	USART_InitStructure.USART_WordLength = USART_StopBits_1;
	USART_InitStructure.USART_Parity = USART_Parity_No;
	USART_InitStructure.USART_Mode = USART_Mode_Rx | USART_Mode_Tx;
	USART_InitStructure.USART_HardwareFlowControl = USART_HardwareFlowControl_None;
	USART_Init(USART2, &USART_InitStructure);
	USART_Cmd(USART2, ENABLE);

	/* Config. interrupts. */
	USART_ITConfig(USART2, USART_IT_RXNE, ENABLE);
	USART_ITConfig(USART2, USART_IT_TXE, ENABLE);
	NVIC_EnableIRQ(USART2_IRQn);

	/* Init. SW queues. */
	osQInit(&usart_rx_q, sizeof(uint8_t), USART_QUEUE_SIZE, usart_rx_data);
	osQInit(&usart_tx_q, sizeof(uint8_t), USART_QUEUE_SIZE, usart_tx_data);
}

void USART2_IRQHandler(void)
{
	/* USART2 receive buffer contains a char. */
	if(USART_GetITStatus(USART2, USART_IT_RXNE) == SET)
	{
		uint8_t data;
		data = USART_ReceiveData(USART2) & 0xFF;
		if(!osEnqueue(&usart_rx_q, (void*)&data))
			THROW_ERROR(E_USART_RX_BUFFER_OVERLOW);
	}

	/* USART2 transmit buffer empty. */
	if(USART_GetITStatus(USART2, USART_IT_TXE) == SET)
	{
		uint8_t data;
		if(osDequeue(&usart_tx_q, &data))
			USART_SendData(USART2, data);
		else
		{
			/* Nothing to send. Disable interrupt. */
			USART_ITConfig(USART2, USART_IT_TXE, DISABLE);
			tx_overflow = 0;
		}
	}
}

static uint8_t usart2PutChar(uint8_t data)
{
	/* Signal, that the buffer has overflowed. */
	if(tx_overflow)
		return 0;
	/* Put data in the q. */
	if(!osEnqueue(&usart_tx_q, (void*)&data))
	{
		tx_overflow = 1;
		return 0;
	}
	/* Enable interrupt. */
	USART_ITConfig(USART2, USART_IT_TXE, ENABLE);
	return 1;
}

static uint8_t usart2GetChar(void)
{
	uint8_t data;
	/* Wait until data arrives. */
	while(!osDequeue(&usart_rx_q, &data)){}
		return data;
}

uint8_t usart2PutString(uint8_t* word, size_t size)
{
	/* Push data as long as it needs that it comes through. */
	for(uint8_t i=0; i<size; i++)
		while(!usart2PutChar(word[i])){}
	/* Did a overflow occur? */
	if(tx_overflow)
	{
		THROW_ERROR(E_USART_RX_BUFFER_OVERLOW);
	}
	return 1;
}

uint8_t usart2GetString(uint8_t* word, size_t buff_size, size_t *string_size)
{
	uint8_t data;
	*string_size = 0;
	do
	{
		data = usart2GetChar();
		if(data == 0)
			return 0;
		usart2PutChar(data);
		if( *string_size < (buff_size-1) )
			word[*string_size] = data;
		else
		{
			THROW_ERROR(E_BUFFER_OVERFLOW);
			return 0;
		}
		(*string_size)++;
	} while( (data != '\r') && (data != '\n') );
	/* Append string termination. */
	word[*string_size] = '\0';
	(*string_size)++;
	return 1;
}

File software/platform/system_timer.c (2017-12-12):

/*
 * system_timer.c
 *
 *  Created on: Dec 6, 2017
 *      Author: maximilian
 */

//--------------Includes-----------------

#include<stm32f10x.h>
#include<stm32f10x_flash.h>
#include<stm32f10x_rcc.h>
#include"../os/scheduler.h"
#include"../os/ossettings.h"

void initAliveLED(void)
{
	/* Activate clock for peripheral. */
	RCC_APB2PeriphClockCmd(RCC_APB2Periph_GPIOA, ENABLE);

	/* Initialize GPIO Pin. */
	GPIO_InitTypeDef GPIO_InitStructure ;
	GPIO_StructInit (&GPIO_InitStructure );
	GPIO_InitStructure.GPIO_Pin = GPIO_Pin_5 ;
	GPIO_InitStructure.GPIO_Mode = GPIO_Mode_Out_PP ;
	GPIO_InitStructure.GPIO_Speed = GPIO_Speed_2MHz ;
	GPIO_Init (GPIOA , & GPIO_InitStructure );
}

void toggleAliveLED(void)
{
	static volatile uint8_t led_stat = 0;
	led_stat = !led_stat;
	GPIO_WriteBit(GPIOA, GPIO_Pin_5, led_stat);
}

void initClock(void)
{
	/* Configure all clocks to max for best performance.
	   If there are EMI, power, or noise problems, try slowing the clocks.*/

	/* First set the flash latency to work with our clock.
	   000 Zero wait state, if 0  MHz < SYSCLK <= 24 MHz
	   001 One wait state, if  24 MHz < SYSCLK <= 48 MHz
	   010 Two wait states, if 48 MHz < SYSCLK <= 72 MHz */
	FLASH_SetLatency(FLASH_Latency_1);

	/* Start with HSI (High-Speed Internal) clock with 8 MHz, divide by 2 and multiply by 9 to
	   get maximum allowed frequency: 36 MHz
	   Enable PLL, wait till it's stable, then select it as system clock*/
	RCC_PLLConfig(RCC_PLLSource_HSI_Div2, RCC_PLLMul_9);
	RCC_PLLCmd(ENABLE);
	while(RCC_GetFlagStatus(RCC_FLAG_PLLRDY) == RESET) {}
	RCC_SYSCLKConfig(RCC_SYSCLKSource_PLLCLK);

	/* Set HCLK, PCLK1, and PCLK2 to SCLK. */
	RCC_HCLKConfig(RCC_SYSCLK_Div1);
	RCC_PCLK1Config(RCC_HCLK_Div8);
	RCC_PCLK2Config(RCC_HCLK_Div8);

	/*  Configure Cortex-M System Tick Timer to tick as the os user defined.*/
	SystemCoreClockUpdate();
	SysTick_Config( (SystemCoreClock/1000) * SYS_TICK_PERIOD_MS );
}

void SysTick_Handler(void)
{
	// TODO: For porting use another timer here to call the scheduler.
	osRunScheduler();
}

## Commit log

2017-06-18 Initial commit.
    [dimensions.scad, pcb_holder_crossbar.scad, pcb_holder_crossbar.stl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]
2017-06-18 Finished CAD work.
    [_saved_led_driver.sch, dimensions.scad, led_driver.kicad_pcb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]
2017-06-18 Added one .gitignore for KiCAD and developed a protection circuit for the LED driver.
    [fourStages.sch, fourStages1.sch, fourStages2.sch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]
2017-06-19 Finished third version of LED driver.
2017-11-12 Started layouting.
    [4Stages1.sch, LEDDriver.sch, fourStages1.sch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]
2017-11-13 LED driver part done.
    [2Stages1.sch, 4Stages1.sch, LEDDriver.sch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]
2017-11-14 Only UI is left for schematics.
    [2Stages1.sch, InterfaceNucleoF103RB.sch, LEDDriver.sch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]
2017-11-14 Almost done with schematics. SPI OLED is missing.
    [2Stages1.sch, InterfaceNucleoF103RB.sch, LEDDriver.sch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]
2017-11-16 No DRC errors anymore in schematics.
    [2Stages1.sch, InterfaceNucleoF103RB.sch, LEDDriver.sch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]
2017-11-19 All components placed.
    [2Stages1.sch, 4Stages1.sch, InterfaceNucleoF103RB.sch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]
2017-11-21 Some progress layouting the beast today.
    [2Stages1.sch, led_driver.kicad_pcb, power.sch]
2017-11-22 Started eliminating DRC errors.
    [2Stages1.sch, InterfaceNucleoF103RB.sch, LEDDriver.sch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]
2017-11-27 Finished layouting the extension board.
    [2Stages1.sch, InterfaceNucleoF103RB.sch, LEDDriver.sch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]
2017-11-27 Added SPI_MISO to SPI interface.
    [2Stages1.sch, InterfaceNucleoF103RB.sch, LEDDriver.sch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]
2017-11-28 Added an adapter board (2 layers).
    [adapter_board-B.Cu.gbr, adapter_board-B.Mask.gbr, adapter_board-B.SilkS.gbr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]
2017-11-30 Changed transistor array of driver for SOT-23 discrete transistor (more dissipation allowed).
    [2Stages1.sch, LEDDriver.sch, UI.sch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]
2017-12-05 Produced Gerber files for both boards. Ready for production.
    [2Stages1.sch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]
2017-12-06 Updated current rating of extension board.
    [extension_board-B.Mask.gbr, extension_board-B.SilkS.gbr, extension_board-Edge.Cuts.gbr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]
2017-12-07 Non-blocking UART driver seems to do its job, also the queues seem to work. No semaphores implemented yet.
2017-12-08 osPrintf works with signed and unsigned integers.
    [2Stages1.sch, InterfaceNucleoF103RB.sch, LEDDriver.sch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]
2017-12-11 Added more OS files to be tracked. Port them now to the STM32.
    [2Stages1.sch, LEDDriver.sch, UI.sch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]
